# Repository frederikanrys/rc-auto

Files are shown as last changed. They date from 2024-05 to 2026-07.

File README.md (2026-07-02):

# Fri3d RC Car

This is a project to build a 3D printed remote controlled car. The car body is based on the classic Volkswagen Bus, reimagined as an off-road RC hot rod. The car is designed to be 3D printed and to be controlled by a remote control.

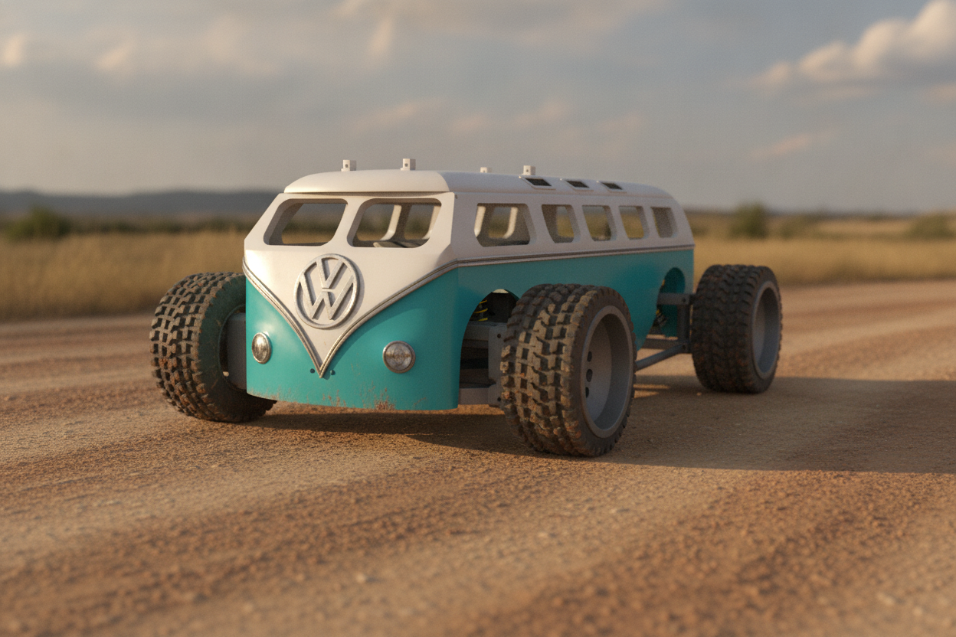
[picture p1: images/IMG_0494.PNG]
VW Bus


## Design Philosophy

The car uses off-the-shelf drivetrain components compatible with **Traxxas Slash 4x4** parts:

- **Differentials** - Metal differentials with bearings
- **Driveshafts** - CVD steel driveshafts and metal center driveshaft
- **Slipper Clutch** - Complete metal slipper clutch assembly
- **Drive Hubs** - Steel drive hub sets

This makes the car durable and easy to repair with widely available RC car parts.

## Parts List

### Motor & Electronics

| Item | Description | Link | Price | Qty |
| --- | --- | --- | ----- | --- |
| Motor + ESC | Pulsar B-20 or B-40 | <a href="https://nl.aliexpress.com/item/1005006742987156.html" target="_blank" rel="noopener noreferrer">AliExpress</a> | ~€30  | 1 |
| Pinion | 12T, 15T, or 20T | <a href="https://www.absima.shop/pp/alu-pinion-32dp/module0-8-20T.htm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" target="_blank" rel="noopener noreferrer">Absima</a> | ~€5 | 1 |
| Battery | 5200mAh, 2S, 80C | <a href="https://www.amazon.de/-/en/dp/B08X4GF9DK" target="_blank" rel="noopener noreferrer">Amazon</a> | ~€30  | 1 |
| Servo | | <a href="https://nl.aliexpress.com/item/1005007301836255.html" target="_blank" rel="noopener noreferrer">AliExpress</a> | ~€10  | 1 |
| Receiver + Transmitter | | | | 1 |

### Drivetrain (Differentials, Driveshafts & Slipper Clutch)

| Item | Description | Link | Price | Qty |
| --- | --- | --- | --- | --- |
| Differential (2pcs) | Front/Rear Differential with Bearing for Slash 4X4 VXL Stampede Rustler | <a href="https://www.aliexpress.com/item/1005007378476905.html" target="_blank" rel="noopener noreferrer">AliExpress</a> | ~€12 | 1 |
| Rear Ring Gear 6879 | Rear Differential Ring Gear G4713 6879 for Traxxas Slash 4X4 | <a href="https://www.aliexpress.com/item/32948469179.html" target="_blank" rel="noopener noreferrer">AliExpress</a> | ~€2 | 1 |
| Front Ring Gear G4513 | Front Differential Ring Gear G4513 for Traxxas Slash 4x4 | <a href="https://www.aliexpress.com/item/32952095481.html" target="_blank" rel="noopener noreferrer">AliExpress</a> | ~€6 | 1 |
| CVD Driveshaft (Front & Rear) | GRC Extreme Heavy Duty CVD U-Joint Steel Driveshaft for Traxxas Slash/Stampede/Hoss/Rustler VXL 4X4 Platinum Ultimate Update Parts, Replace #6851 - used for both front and rear (sold in packs of 2, need 2 packs) | <a href="https://www.temu.com/goods.html?goods_id=605796830151694&sku_id=92876117669400" target="_blank" rel="noopener noreferrer">Temu</a> | ~€13.50/pack | 2 |
| Center Driveshaft 6855 | Metal Center Driveshaft 6855 for Traxxas Slash 4X4 4WD Rally (Red) | <a href="https://www.aliexpress.com/item/1005005894739029.html" target="_blank" rel="noopener noreferrer">AliExpress</a> | ~€3 | 1 |
| Drive Hub Set Front | Steel Drive Hub Set for Traxxas Slash 4X4 VXL/Rustler/Stampede/XO-1 (**Front** **only**) | <a href="https://www.aliexpress.com/item/1005009469068869.html" target="_blank" rel="noopener noreferrer">AliExpress</a> | ~€2 | 1 |
| Slipper Clutch | Complete Slipper Clutch Assembly for Traxxas Slash Stampede 4X4 Rally | <a href="https://www.aliexpress.com/item/1005007927630121.html" target="_blank" rel="noopener noreferrer">AliExpress</a> | ~€8 | 1 |
| Motor Mount | Adjustable Motor Mounting Bracket Holder for 540/3660/3650 Brushless Motors | <a href="https://nl.aliexpress.com/item/4000424368907.html" target="_blank" rel="noopener noreferrer">AliExpress</a> | ~€4 | 1 |

### Bearings

| Item | Description | Link | Price | Qty |
| ---- | --- | ---- | ----- | --- |
| Bearing 5x11x4mm | MR115-2RS Bearing 10pcs 5x11x4mm Steel Double Shielded | <a href="https://nl.aliexpress.com/item/32824707297.html" target="_blank" rel="noopener noreferrer">AliExpress</a> | ~€4 | 1 |
| Bearing 6x12x4mm | MR126RS Bearing 10pcs 6x12x4mm ABEC-7 Blue Sealed | <a href="https://www.aliexpress.com/item/1005006083328247.html" target="_blank" rel="noopener noreferrer">AliExpress</a> | ~€4 | 1 |
| Bearing 10x15x4mm | 6700-2RS Bearing 10pcs 10x15x4mm ABEC-3 Blue Sealed | <a href="https://nl.aliexpress.com/item/32904604356.html" target="_blank" rel="noopener noreferrer">AliExpress</a> | ~€4 | 1 |
| Bearing 12x18x4mm | 6701-2RS Bearing 10pcs 12x18x4mm ABEC-7 Blue Sealed | <a href="https://www.aliexpress.com/item/1005006475668561.html" target="_blank" rel="noopener noreferrer">AliExpress</a> | ~€4 | 1 |

### Fasteners & Hardware

| Item | Description | Link | Price | Qty |
| --- | --- | --- | ----- | --- |
| Screw Bolt Set M3 | M2 M3 M4 Screw Bolt Set for RC Crawler Bumper Driveshaft Pin | <a href="https://www.aliexpress.com/item/1005009800470993.html" target="_blank" rel="noopener noreferrer">AliExpress</a> | ~€2 | 1 |
| Lock Nuts M5 | 304/316 Stainless Steel Flange Nylon Lock Nuts M5 Serrated (20pcs) | <a href="https://www.aliexpress.com/item/1005009771309255.html" target="_blank" rel="noopener noreferrer">AliExpress</a> | ~€2 | 1 |
| Dowel Pins M2 | GB119 Cylindrical Dowel Pins M2 304 Stainless Steel (50pcs, 10mm)  | <a href="https://www.aliexpress.com/item/1005007023343232.html" target="_blank" rel="noopener noreferrer">AliExpress</a> | ~€2 | 1 |
| Heat Insert Nuts M3 | Brass Heat Insert Nuts M3xL5xOD4.5 for 3D Printing (50pcs) | <a href="https://www.aliexpress.com/item/1005006472702418.html" target="_blank" rel="noopener noreferrer">AliExpress</a> | ~€2 | 1 |
| Screws M3 | M3 Hex Socket Screws Set (440pcs) | <a href="https://www.amazon.de/-/nl/dp/B0B3MGZ7T2" target="_blank" rel="noopener noreferrer">Amazon</a> | ~€10  | 1 |
| Body Shell Clips | MJX Hyper Go R-type Body Shell Clips Pin (24pcs) | <a href="https://www.aliexpress.com/item/1005009096269708.html" target="_blank" rel="noopener noreferrer">AliExpress</a> | ~€2 | 1 |

## Printed Parts

Depending on the print settings, you will need around 2KG of Filament to print all the parts. Instead of PLA, you can also use PETG or ABS.

For TPU parts (except tires), we recommend <a href="https://extrudr.com/en/at/products/flex-hard/" target="_blank" rel="noopener noreferrer">Extrudr Flex Hard</a> for better impact absorption.

| Part | Material | Qty | Notes |
|---|---|-----|---|
| <a href="files/plate-front-bottom.stl" target="_blank" rel="noopener noreferrer">Plate - front - bottom</a> | PLA | 1 | |
| <a href="files/plate-rear-bottom.stl" target="_blank" rel="noopener noreferrer">Plate - rear - bottom</a> | PLA | 1 | |
| <a href="files/plate-diff-front-top.stl" target="_blank" rel="noopener noreferrer">Plate - diff - front - top</a> | PLA | 1 | **100% infill** |
| <a href="files/plate-diff-rear-top.stl" target="_blank" rel="noopener noreferrer">Plate - diff - rear - top</a> | PLA | 1 | **100% infill** |
| <a href="files/plate-battery-holder.stl" target="_blank" rel="noopener noreferrer">Plate - battery - holder</a> | PLA | 1 | |
| <a href="files/wing-bottom.stl" target="_blank" rel="noopener noreferrer">Wing - bottom</a> | PLA/TPU-A98 | 4 | TPU for impact |
| <a href="files/wing-top.stl" target="_blank" rel="noopener noreferrer">Wing - top</a> | PLA/TPU-A98 | 4 | TPU for impact |
| <a href="files/turn-caster-front.stl" target="_blank" rel="noopener noreferrer">Turn - caster - front</a> | PLA | 2 | **100% infill** |
| <a href="files/turn-caster-rear.stl" target="_blank" rel="noopener noreferrer">Turn - caster - rear</a> | PLA | 2 | **100% infill** |
| <a href="files/turn-front.stl" target="_blank" rel="noopener noreferrer">Turn - front</a> | PLA | 2 | **100% infill** |
| <a href="files/steering-left.stl" target="_blank" rel="noopener noreferrer">Steering - left</a> | PLA | 1 | |
| <a href="files/steering-right.stl" target="_blank" rel="noopener noreferrer">Steering - right</a> | PLA | 1 | |
| <a href="files/steering-connect.stl" target="_blank" rel="noopener noreferrer">Steering - connector</a> | PLA/TPU-A95 | 1 | TPU = servo saver |
| <a href="files/steering-rings.stl" target="_blank" rel="noopener noreferrer">Steering - rings</a> | PLA | 2 | |
| <a href="files/steering-top.stl" target="_blank" rel="noopener noreferrer">Steering - top</a> | PLA | 1 | |
| <a href="files/steering-arm-75mm.stl" target="_blank" rel="noopener noreferrer">Steering - rod - 75mm</a> | PLA/TPU-A95 | 2 | TPU = servo saver |

### VW Bus Body

| Part | Material | Qty | Notes |
|---|---|-----|---|
| <a href="files/vw-bus/bus-front.3mf" target="_blank" rel="noopener noreferrer">Bus - front</a> | PLA/PETG | 1 | |
| <a href="files/vw-bus/bus-rear.3mf" target="_blank" rel="noopener noreferrer">Bus - rear</a> | PLA/PETG | 1 | |
| <a href="files/vw-bus/roof-front.stl" target="_blank" rel="noopener noreferrer">Roof - front</a> | PLA/PETG | 1 | |
| <a href="files/vw-bus/roof-rear.stl" target="_blank" rel="noopener noreferrer">Roof - rear</a> | PLA/PETG | 1 | |
| <a href="files/vw-bus/nose.stl" target="_blank" rel="noopener noreferrer">Nose</a> | PLA/PETG | 1 | |
| <a href="files/vw-bus/logo.stl" target="_blank" rel="noopener noreferrer">Logo</a> | PLA/PETG | 1 | |
| <a href="files/vw-bus/light.stl" target="_blank" rel="noopener noreferrer">Light</a> | PLA/PETG | 1 | |
| <a href="files/vw-bus/rail-nose-left.stl" target="_blank" rel="noopener noreferrer">Rail - nose - left</a> | PLA/PETG | 1 | |
| <a href="files/vw-bus/rail-nose-right%20.stl" target="_blank" rel="noopener noreferrer">Rail - nose - right</a> | PLA/PETG | 1 | |
| <a href="files/vw-bus/rail-front-left.stl" target="_blank" rel="noopener noreferrer">Rail - front - left</a> | PLA/PETG | 1 | |
| <a href="files/vw-bus/rail-front-right.stl" target="_blank" rel="noopener noreferrer">Rail - front - right</a> | PLA/PETG | 1 | |
| <a href="files/vw-bus/rail-rear-left%20.stl" target="_blank" rel="noopener noreferrer">Rail - rear - left</a> | PLA/PETG | 1 | |
| <a href="files/vw-bus/rail-rear-right.stl" target="_blank" rel="noopener noreferrer">Rail - rear - right</a> | PLA/PETG | 1 | |

### Optional Printed Parts

These parts can also be bought off the shelf.

| Part | Material | Qty | Notes |
|---|---|-----|---|
| <a href="files/shock.stl" target="_blank" rel="noopener noreferrer">Shock</a> | PLA | 8 | Slider and cap |
| <a href="files/wheel-tire.stl" target="_blank" rel="noopener noreferrer">Wheel - tire</a> | TPU-A95 | 4 | |
| <a href="files/wheel-rim.stl" target="_blank" rel="noopener noreferrer">Wheel - rim</a> | PLA | 4 | |
| <a href="files/wheel-hex.stl" target="_blank" rel="noopener noreferrer">Wheel - hex</a> | PLA | 4 | |

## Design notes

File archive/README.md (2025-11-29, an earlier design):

# Fri3d RC Car (Archive)

> **Note:** This is the archived version of the original Fri3d RC Car design. For the latest version with Traxxas Slash 4x4 compatible drivetrain components, see the [main project](../README.md).

This is a project to build a 3D printed remote controlled car. The car body is based on the [Cybertruck](https://www.tesla.com/cybertruck) from Tesla. The car is designed to be 3D printed and to be controlled by a remote control.

As this is not a beginner project, it is recommended to have some experience with 3D printing and remote controlled cars.
The project is an open-source project and can be used by anyone. We originally designed this project for [Fri3d Camp](https://fri3d.be/) to build 5 cars with children and play with them during the camp.

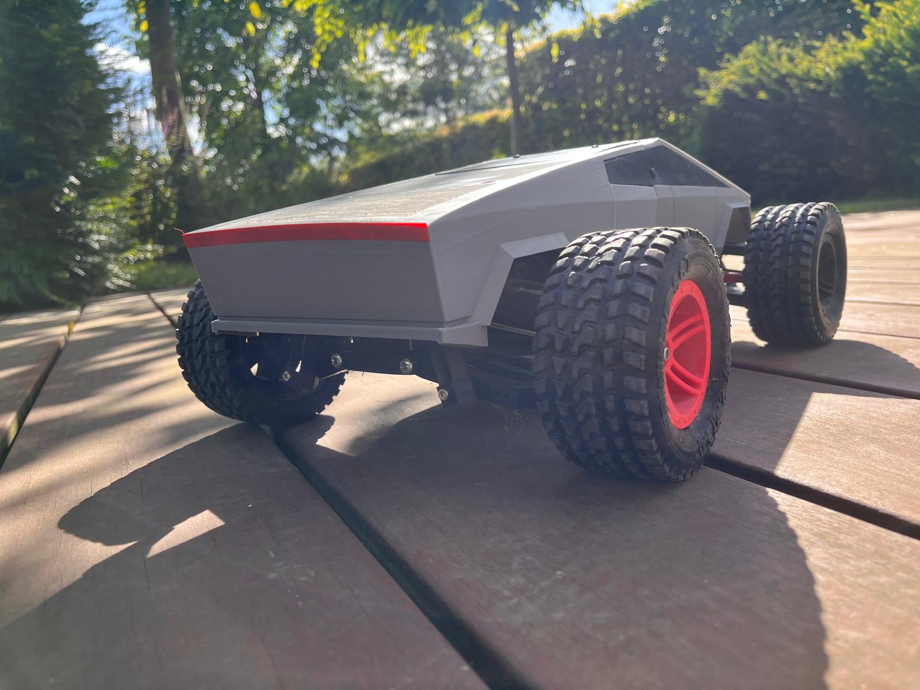
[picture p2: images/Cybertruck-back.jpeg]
Cybertruck


# How to start?
There is a combination of printed parts and off the shelf parts. Both off the shelf parts and printed parts are listed in the [Bill of Material](#Bill-of-Material). Off the shelf parts can be bought from various online stores such as the one proposed in the Link column.
The printed parts are available in the [stl](stl) directory. The original design files are available in the [shapr](shapr) directory.
The printed parts can be printed on a printer with a maximum size of 25cm x 25cm x 25cm. Most parts can be printed with PLA, but some parts are to be printed with TPU (to absorb impact).

The car is designed with durability in mind. You will notice we do not print the parts that need to be very strong such as the differentials and dog bones. You should buy them online. It makes the car a bit more expensive to build, but it will last much longer. 
For more durability, some parts are to be printed in TPU (flexible filament). i.e.: the bumper, the caster claws, and the top and bottom of the wings,... 
That way, they can absorb the impact of a crash without breaking.

# Assembly
Once you have the printed the parts on your printer and bought some of the parts online, you can start to assemble the car as described in the following documents:
1. [Part 1 - Body](manual/part1-body.pdf) 
2. [Part 2 - Front & Back](manual/part2-front-back.pdf)
3. [Part 3 - Final](manual/part3-final.pdf)

Happy assembling and Good Luck!

# Bill of Material
## Off the shelf parts
| Description | # | Comment | Link |
| --- | --- | --- | --- |
| Motor + ESC | 1 | Test Pulsar B-20, B-40 | [aliexpress.com](https://nl.aliexpress.com/item/1005006742987156.html) |
| Motor Mount | 1 | | |
| Pinion | 1 | 12T, 15T, 20T | [absima.be](https://www.absima.shop/pp/alu-pinion-32dp/module0-8-20T.htm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) |
| Battery | 1 | 5200mAh, 2S, 80C | [amazon.de](https://www.amazon.de/-/en/dp/B08X4GF9DK?psc=1&ref=ppx_yo2ov_dt_b_product_details) |
| Servo | 1 | | [aliexpress.com](https://nl.aliexpress.com/item/1005007301836255.html) |
| Receiver + Transmitter | 1 | | |
| Bearing - 10X15X4 | 8 | | |
| Bearing - 5X10X4 | 8 | | |
| Screws M3 | 1 | 440 pieces | [Amazon.de](https://www.amazon.de/-/nl/dp/B0B3MGZ7T2/ref=pd_day0fbt_thbs_d_sccl_2/257-0877788-9470555) |
| Screws M4 (100mm or 70mm) | 4 | Bottom wing - plate connection | |
| Wheel Fastener | 4 | | |
| Threaded inserts | 8 | Diff cover | |
| Rubber band | 4 | Shock | |

## Printed parts
Depending on the print settings, you will need around 2KG of Filament to print all the parts. Instead of PLA, you can also use PETG or ABS.

| Check | Description | Material | # | Comment |
| --- | --- | --- | --- | --- |
| <span style="color: green;">&#10004;</span> | Receiver box | PLA | 1 | Will use OOTB |
| | Servo - steering rod | | 1 | |
| | | | | |
| <span style="color: green;">&#10004;</span> | [Wheel - tire](stl/wheel-tire.stl) | TPU-A95 | 4 | Last set of 4 are from test vehicle |
| <span style="color: green;">&#10004;</span> | [Wheel - rim](stl/wheel-rim.stl) | PLA | 4 | Last set of 4 are from test vehicle |
| | [Wheel - hex](stl/wheel-hex.stl) | PLA | 4 | Still need to make 2mmx1cm hex pins |
| <span style="color: green;">&#10004;</span> | [Plate - center](stl/plate-center.stl) | PLA | 1 | 3 cannot handle long M4 x 100mm, 2 have a minor defect on top |
| <span style="color: green;">&#10004;</span> | [Plate - front](stl/plate-bottom-front.stl) | PLA | 1 | |
| <span style="color: green;">&#10004;</span> | [Plate - rear](stl/plate-bottom-rear.stl) | PLA | 1 | |
| <span style="color: green;">&#10004;</span> | [Plate - Diff - top](stl/plate-diff-top.stl) | PLA | 2 | Print with 100% fill rate |
| <span style="color: green;">&#10004;</span> | [Plate - battery - holder](stl/plate-battery-holder.stl) | PLA | 1 | |
| <span style="color: green;">&#10004;</span> | [Wing - bottom](stl/wing-bottom.stl) | PLA or TPU-A98 | 4 | Use TPU to absorb impact |
| <span style="color: green;">&#10004;</span> | [Wing - top](stl/wing-top.stl) | PLA or TPU-A98 | 4 | Use TPU to absorb impact |
| | [Caster - claw](stl/turn-caster) | TPU-A98 | 4 | Use TPU to absorb impact |
| | [Caster - turning](stl/turn-front) | PLA | 2 | |
| | [Caster - fixed](stl/turn-rear) | PLA | 2 | |
| <span style="color: green;">&#10004;</span> | [Shock - slider](stl/Shock.stl) | PLA | 8 | |
| <span style="color: green;">&#10004;</span> | [Shock - cap](stl/Shock.stl) | PLA | 8 | |
| <span style="color: green;">&#10004;</span> | [Steer - turn-left](stl/steering-left.stl) | PLA | 1 | |
| <span style="color: green;">&#10004;</span> | [Steer - turn-right](stl/steering-right.stl) | PLA | 1 | |
| <span style="color: green;">&#10004;</span> | [Steer - connector](stl/steering-connect.stl) | PLA or TPU-A95 | 1 | TPU acts as servo saver |
| <span style="color: green;">&#10004;</span> | [Steer - rings](stl/steering-rings.stl) | PLA | 2 | |
| <span style="color: green;">&#10004;</span> | [Steer - top](stl/steering-top.stl) | PLA | 1 | |
| <span style="color: green;">&#10004;</span> | [Steer - rod - 67mm](stl/steering-arm-67mm.stl) | PLA or TPU-A95 | 2 | TPU acts as servo saver |
| <span style="color: green;">&#10004;</span> | [Driveshaft - bearing](stl/driveshaft-bearing-28x12.5x8.stl) | PLA | 1 | |
| | [Driveshaft - gear 48T](stl/driveshaft-gear-48T.stl) | PLA | 1 | Print with 100% fill rate |
| <span style="color: green;">&#10004;</span> | [Driveshaft - gear 60T](stl/driveshaft-gear-60T.stl) | PLA | 1 | Print with 100% fill rate |
| <span style="color: green;">&#10004;</span> | [Driveshaft - axle](stl/driveshaft.stl) | PLA or ABS | 1 | Print with 100% fill rate |
| <span style="color: green;">&#10004;</span> | [Bumper](stl/bumper.stl) | TPU-A95 | 1 | Use TPU to absorb impact |
| <span style="color: green;">&#10004;</span> | [Cybertruck - front](stl/Cybertruck-front.stl) | PLA | 1 | |
| <span style="color: green;">&#10004;</span> | [Cybertruck - front - holder](stl/Cybertruck-front-holder.stl) | PLA | 1 | |
| <span style="color: green;">&#10004;</span> | [Cybertruck - rear](stl/Cybertruck-rear.stl) | PLA | 1 | |
| <span style="color: green;">&#10004;</span> | [Cybertruck - rear - holder](stl/Cybertruck-rear-holder.stl) | PLA | 1 | |
| <span style="color: green;">&#10004;</span> | [Cybertruck - decal](stl/Cybertruck-decal.stl) | PLA | 1 | |
| <span style="color: green;">&#10004;</span> | [Cybertruck - logo](stl/Cybertruck-logo.stl) | PLA | 1 | |

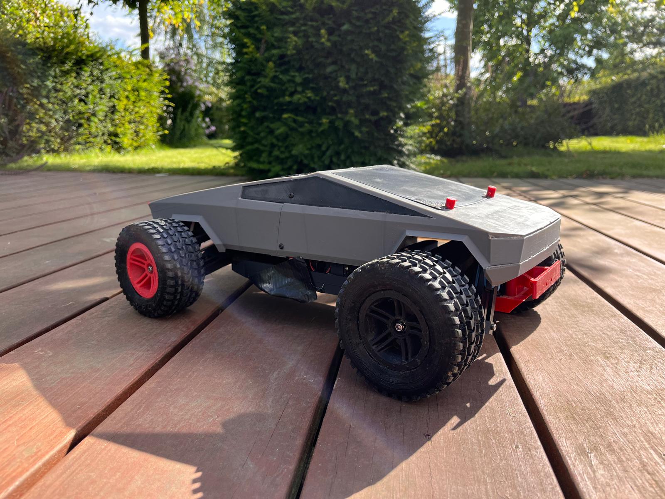
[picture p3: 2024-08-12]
images/Cybertruck-front.jpeg

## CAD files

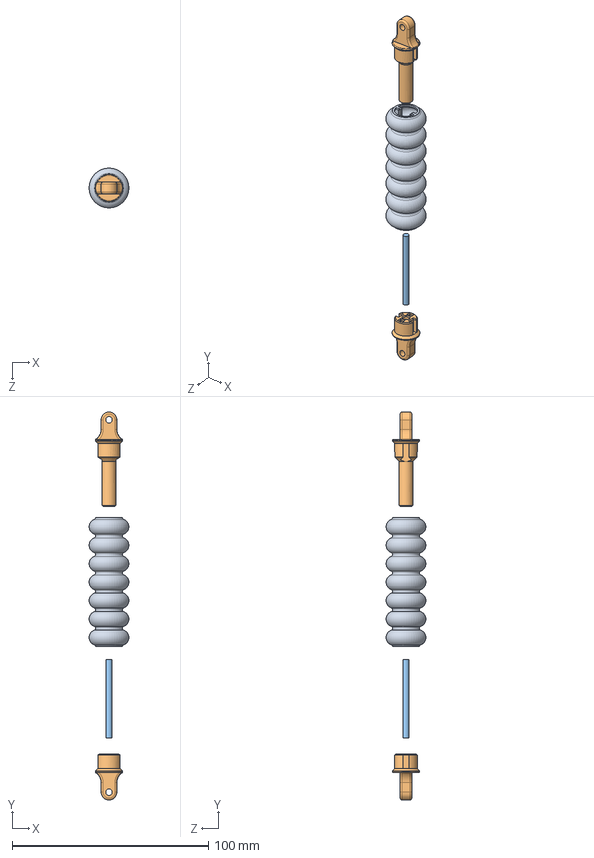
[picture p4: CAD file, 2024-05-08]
shapr/shocks/TPU Shocks/shock-assy-V2.SLDASM
20.3 x 197.6 x 20.3 mm
tpu-spring
shock-eye x 2
shock-pin

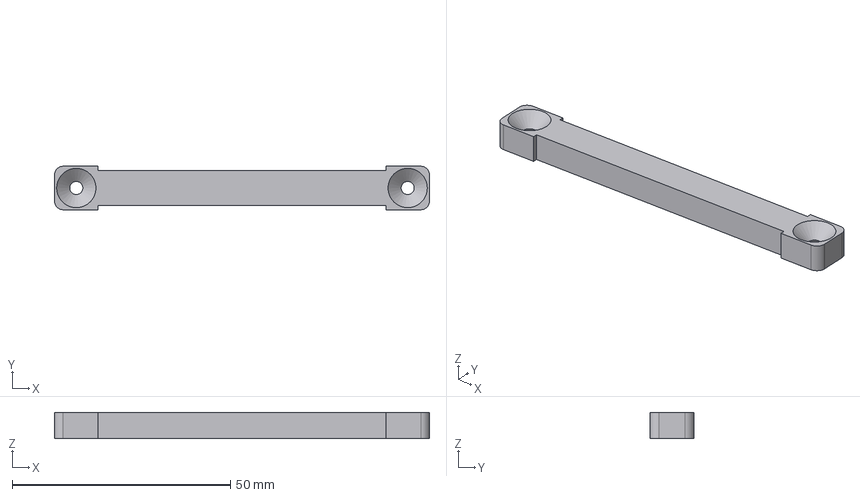
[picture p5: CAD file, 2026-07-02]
files/originals/SteerArm.step
86.0 x 10.0 x 6.00 mm

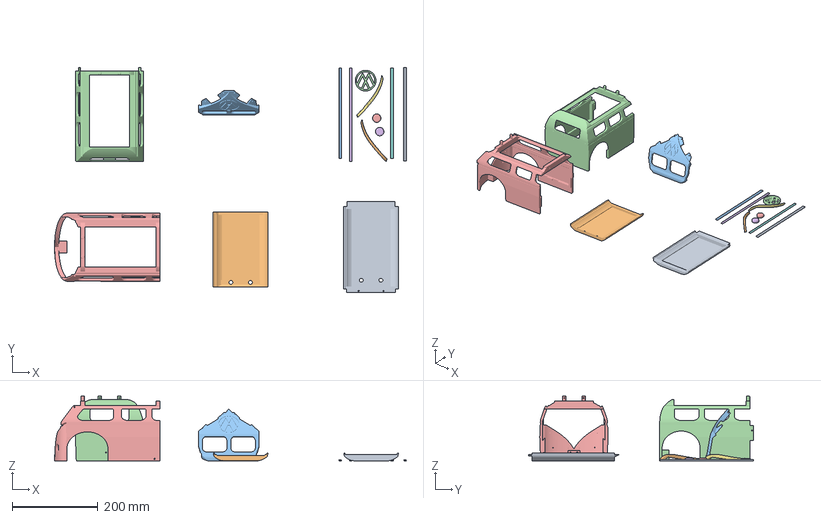
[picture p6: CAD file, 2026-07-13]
files/vw-bus/vw-bus-print-plate.3mf
821.7 x 525.9 x 151.5 mm
roof-rear.stl
roof-front.stl
nose.stl
bus-rear
bus-front
rail-front-right.stl
rail-nose-right .stl
rail-rear-right.stl
rail-front-left.stl
rail-nose-left.stl
rail-rear-left .stl
logo.stl
light.stl x 2

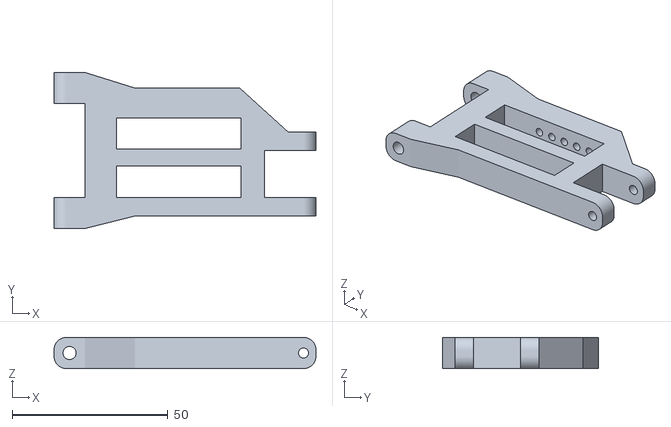
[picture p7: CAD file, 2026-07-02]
files/wing-bottom.stl
84.0 x 50.0 x 10.0

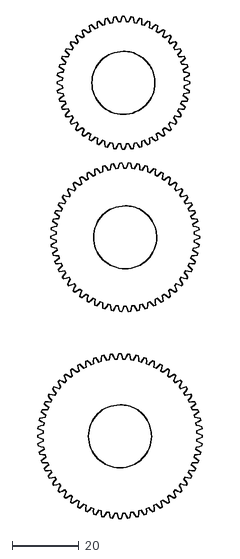
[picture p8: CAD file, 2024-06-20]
shapr/util/gears.dxf
49.3 x 150.4

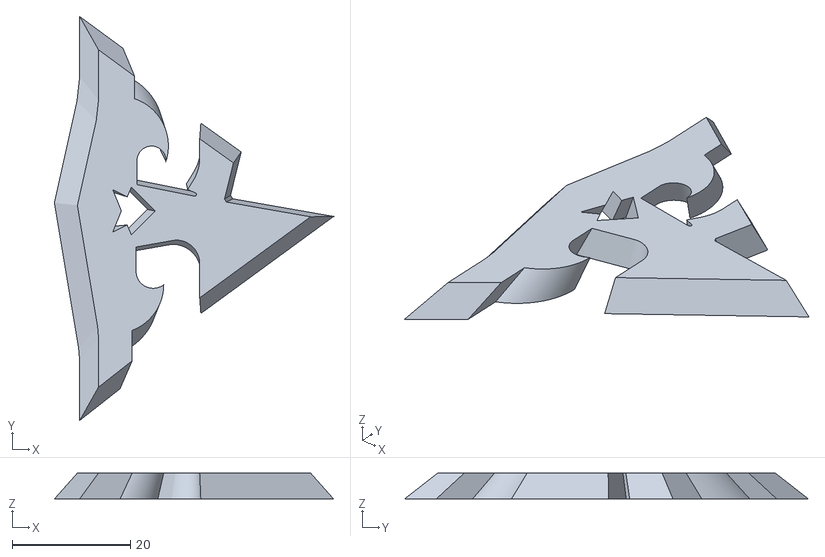
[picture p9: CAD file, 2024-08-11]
stl/Cybertruck-logo.stl
47.3 x 68.5 x 4.40

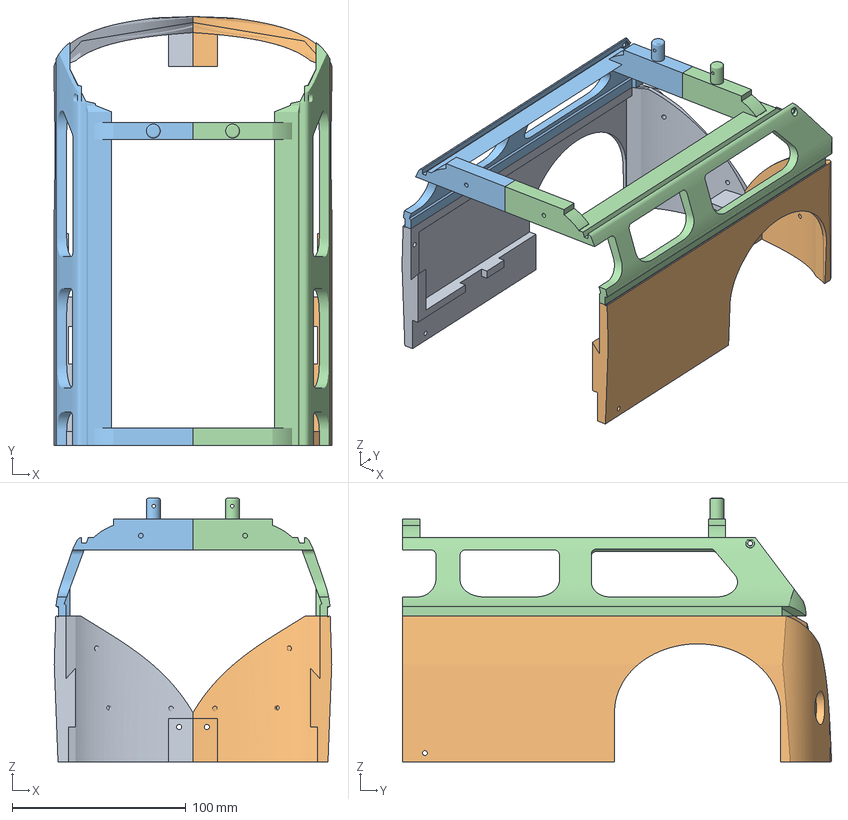
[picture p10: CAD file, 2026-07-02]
files/vw-bus/bus-front.3mf
159.6 x 246.7 x 151.5 mm

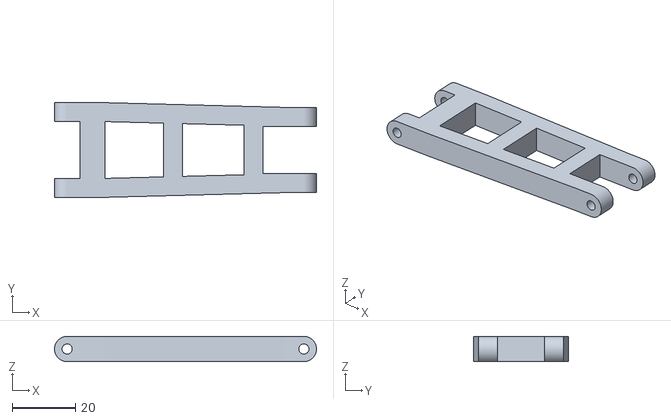
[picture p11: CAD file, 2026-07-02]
files/wing-top.stl
83.0 x 30.0 x 8.00

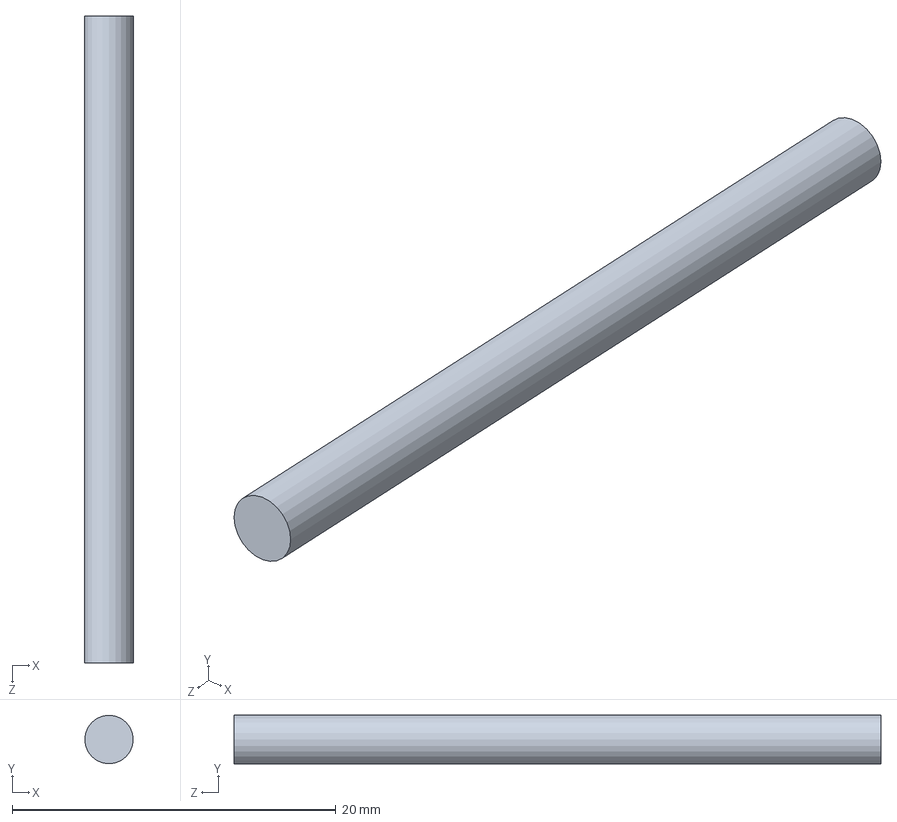
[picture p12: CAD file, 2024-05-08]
shapr/shocks/TPU Shocks/shock-pin.SLDPRT
3.00 x 3.00 x 40.0 mm

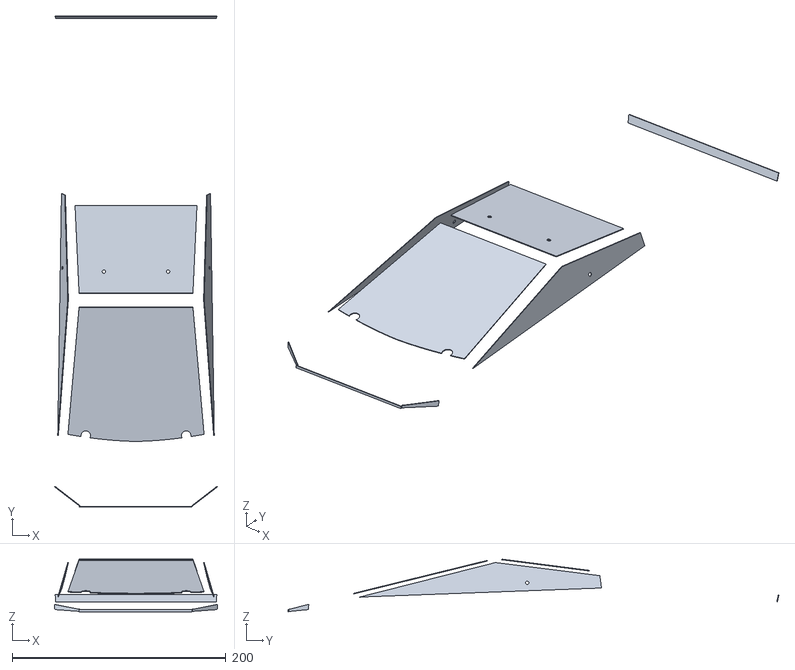
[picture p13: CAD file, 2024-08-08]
stl/Cybertruck-decal.stl
152.7 x 459.8 x 49.4

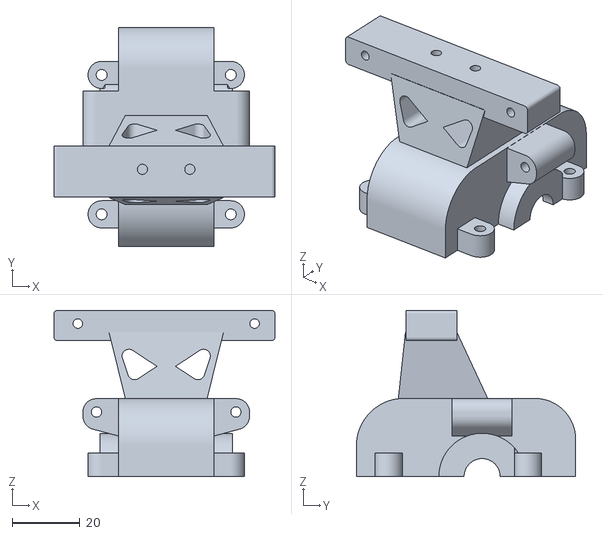
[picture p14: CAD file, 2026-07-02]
files/plate-diff-rear-top.stl
65.0 x 64.5 x 48.9

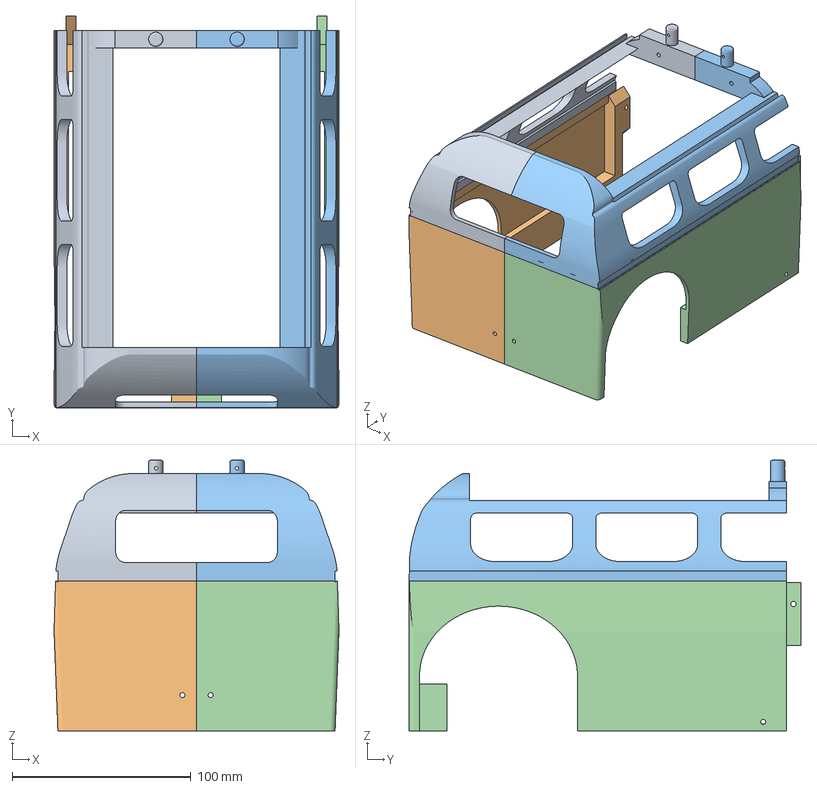
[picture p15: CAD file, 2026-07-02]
files/vw-bus/bus-rear.3mf
159.6 x 219.4 x 151.5 mm

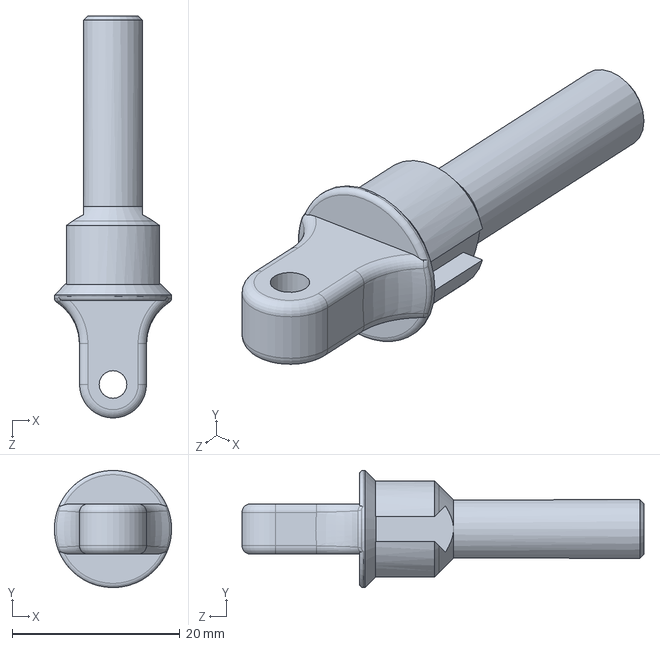
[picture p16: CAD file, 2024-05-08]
shapr/shocks/TPU Shocks/shock-eye.SLDPRT
14.0 x 14.0 x 48.0 mm

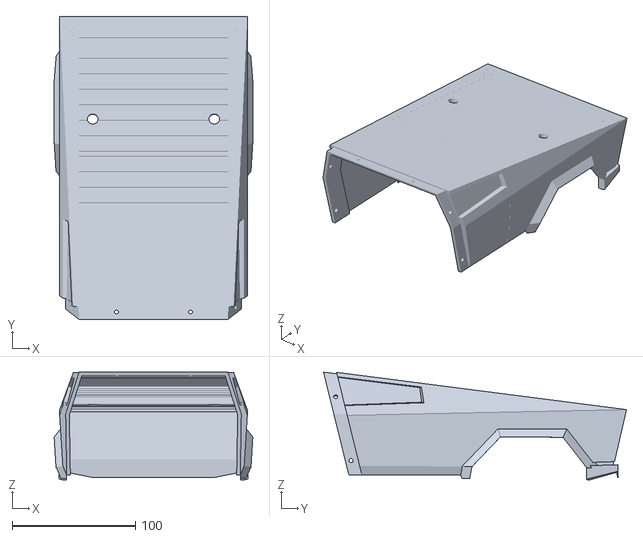
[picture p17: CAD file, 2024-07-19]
stl/Cybertruck-rear.stl
161.3 x 246.0 x 87.5

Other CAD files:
files/plate-rear-bottom.stl
files/vw-bus/logo.stl
stl/plate-center.stl
files/turn-caster-front.stl
archive/shapr/shocks/OpenRC Shocks/STL/Body.stl
archive/shapr/shocks/OpenRC Shocks/STL/Bottom.stl
archive/shapr/shocks/OpenRC Shocks/STL/Lid.stl
archive/shapr/shocks/OpenRC Shocks/STL/Spring.stl
archive/shapr/shocks/OpenRC Shocks/STP/Body.stp
archive/shapr/shocks/OpenRC Shocks/STP/Bottom.stp
archive/shapr/shocks/OpenRC Shocks/STP/Lid.stp
archive/shapr/shocks/OpenRC Shocks/STP/Open RC Experimental Shock Assembly.stp
archive/shapr/shocks/OpenRC Shocks/STP/Spring.stp
archive/shapr/shocks/TPU Shocks/shock-assy.SLDDRW
archive/stl/Cybertruck-front-holder.stl
archive/stl/Cybertruck-front.stl
archive/stl/Cybertruck-rear-holder.stl
archive/stl/driveshaft-gear-48T.stl
archive/stl/driveshaft-gear-60T.stl
archive/stl/driveshaft.stl
archive/stl/plate-bottom-front.stl
archive/stl/plate-bottom-rear.stl
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

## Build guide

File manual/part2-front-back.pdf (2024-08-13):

# FR0NT

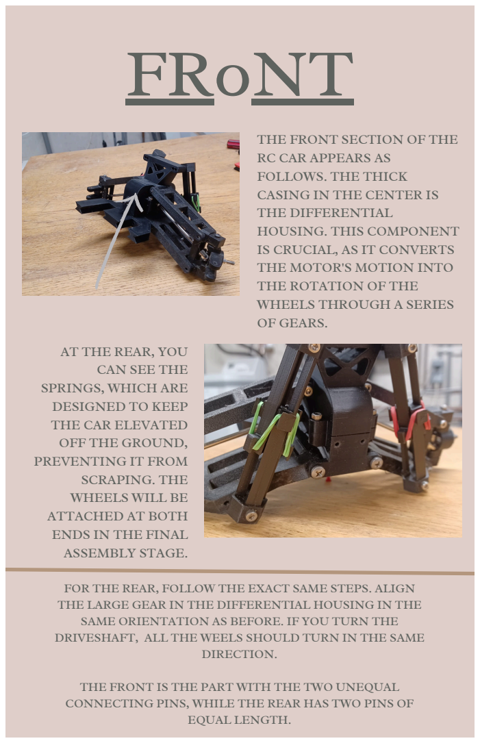
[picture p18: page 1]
DIRECTION.; EQUAL LENGTH.

THE FRONT SECTION OF THE
RC CAR APPEARS AS
FOLLOWS. THE THICK
CASING IN THE CENTER IS
THE DIFFERENTIAL
HOUSING. THIS COMPONENT
IS CRUCIAL, AS IT CONVERTS
THE MOTOR'S MOTION INTO
THE ROTATION OF THE
WHEELS THROUGH A SERIES
OF GEARS.

AT THE REAR, YOU
CAN SEE THE

SPRINGS, WHICH ARE
DESIGNED TO KEEP
THE CAR ELEVATED
OFF THE GROUND,
PREVENTING IT FROM
SCRAPING. THE
WHEELS WILL BE
ATTACHED AT BOTH
ENDS IN THE FINAL
ASSEMBLY STAGE.

FOR THE REAR, FOLLOW THE EXACT SAME STEPS. ALIGN
THE LARGE GEAR IN THE DIFFERENTIAL HOUSING IN THE
SAME ORIENTATION AS BEFORE. IF YOU TURN THE
DRIVESHAFT, ALL THE WEELS SHOULD TURN IN THE SAME

THE FRONT IS THE PART WITH THE TWO UNEQUAL
CONNECTING PINS, WHILE THE REAR HAS TWO PINS OF

# STEP 1

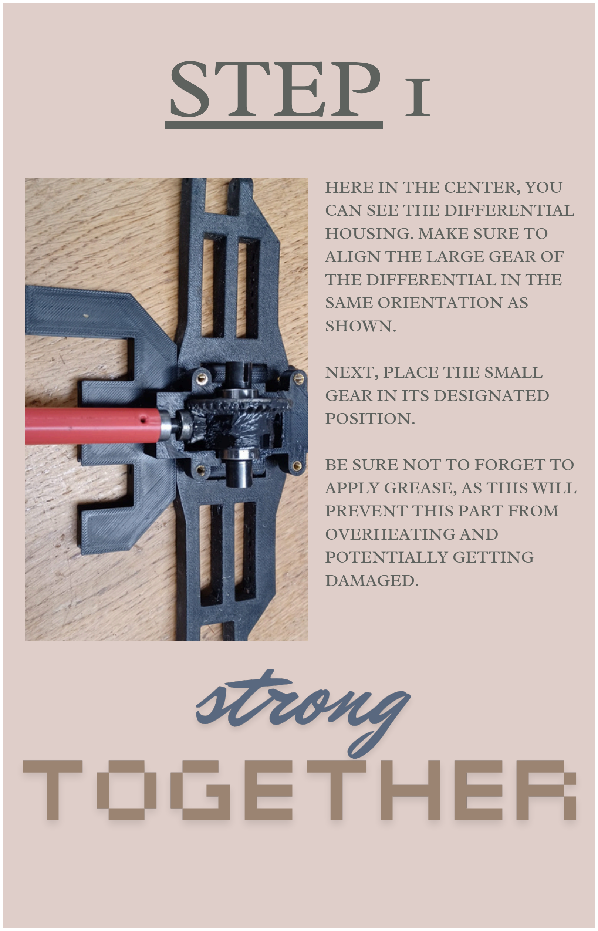
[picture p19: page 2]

HERE IN THE CENTER, YOU
CAN SEE THE DIFFERENTIAL
HOUSING. MAKE SURE TO
ALIGN THE LARGE GEAR OF
THE DIFFERENTIAL IN THE
SAME ORIENTATION AS
SHOWN.

NEXT, PLACE THE SMALL
GEAR IN ITS DESIGNATED
POSITION.

BE SURE NOT TO FORGET TO
APPLY GREASE, AS THIS WILL PREVENT THIS PART FROM
OVERHEATING AND
POTENTIALLY GETTING
DAMAGED.

# STEP 2

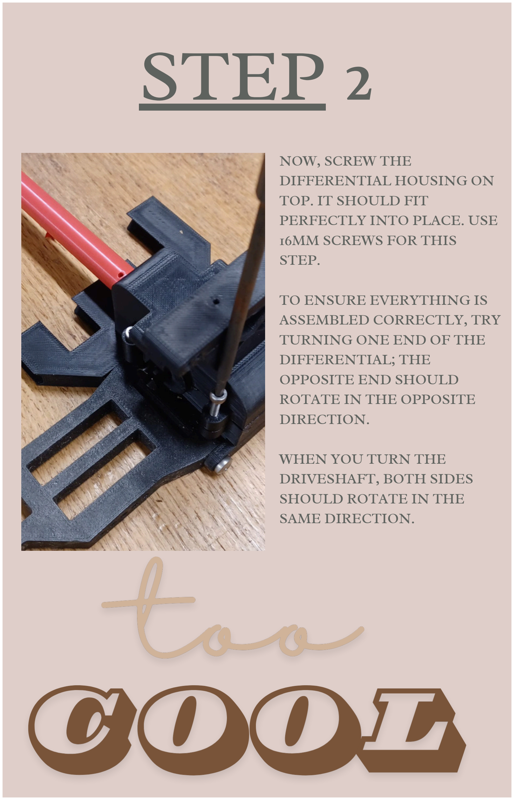
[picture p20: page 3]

NOW, SCREW THE
DIFFERENTIAL HOUSING ON
TOP. IT SHOULD FIT
PERFECTLY INTO PLACE. USE
16MM SCREWS FOR THIS
STEP.

TO ENSURE EVERYTHING IS
ASSEMBLED CORRECTLY, TRY
TURNING ONE END OF THE
DIFFERENTIAL; THE
OPPOSITE END SHOULD
ROTATE IN THE OPPOSITE
DIRECTION.

WHEN YOU TURN THE
DRIVESHAFT, BOTH SIDES
SHOULD ROTATE IN THE
SAME DIRECTION.

# STEP 3

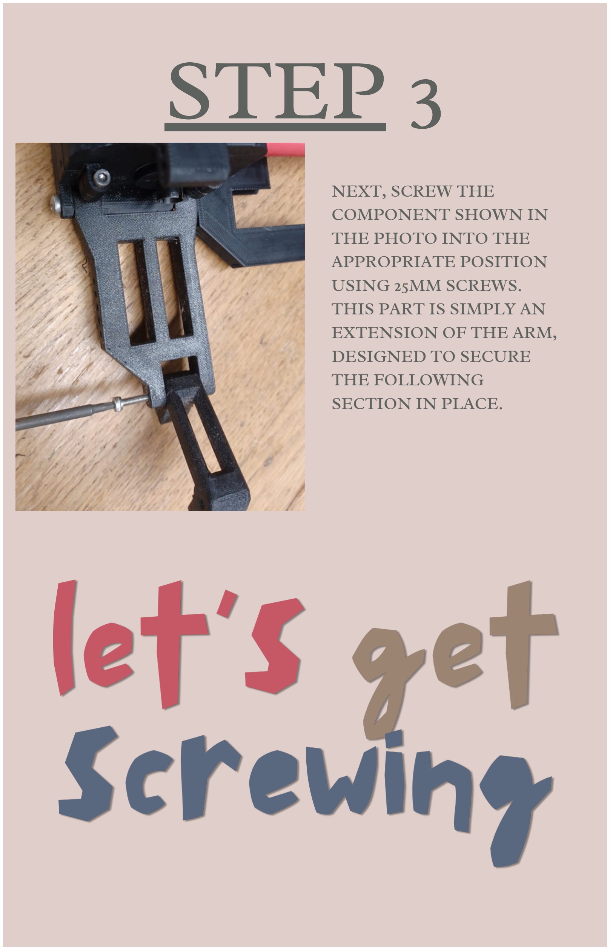
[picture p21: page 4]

NEXT, SCREW THE
COMPONENT SHOWN IN
THE PHOTO INTO THE
APPROPRIATE POSITION
USING 25MM SCREWS.
THIS PART IS SIMPLY AN
EXTENSION OF THE ARM,
DESIGNED TO SECURE
THE FOLLOWING
SECTION IN PLACE.

# STEP 4

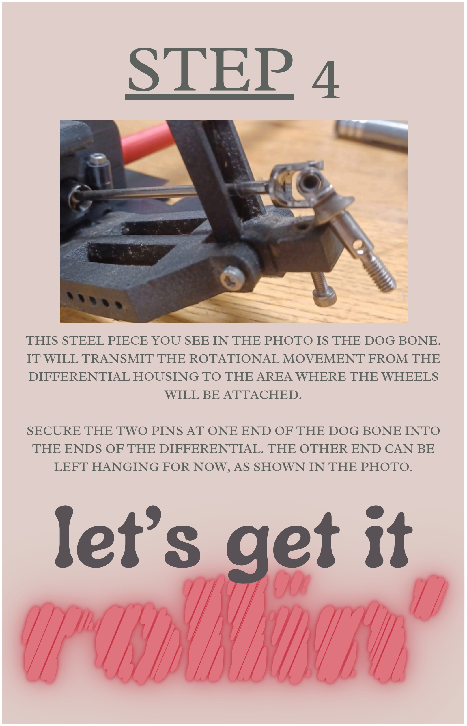
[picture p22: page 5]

THIS STEEL PIECE YOU SEE IN THE PHOTO IS THE DOG BONE. IT WILL TRANSMIT THE ROTATIONAL MOVEMENT FROM THE DIFFERENTIAL HOUSING TO THE AREA WHERE THE WHEELS WILL BE ATTACHED.

SECURE THE TWO PINS AT ONE END OF THE DOG BONE INTO THE ENDS OF THE DIFFERENTIAL. THE OTHER END CAN BE LEFT HANGING FOR NOW, AS SHOWN IN THE PHOTO.

# let’s get it

# STEP 5

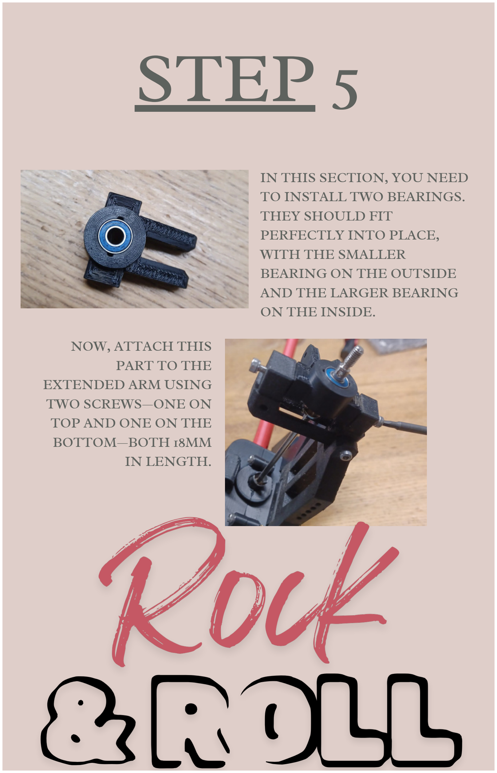
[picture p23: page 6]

IN THIS SECTION, YOU NEED
TO INSTALL TWO BEARINGS.
THEY SHOULD FIT
PERFECTLY INTO PLACE,
WITH THE SMALLER
BEARING ON THE OUTSIDE
AND THE LARGER BEARING
ON THE INSIDE.

NOW, ATTACH THIS
PART TO THE
EXTENDED ARM USING
TWO SCREWS—ONE ON
TOP AND ONE ON THE
BOTTOM—BOTH 18MM
IN LENGTH.

# STEP 6

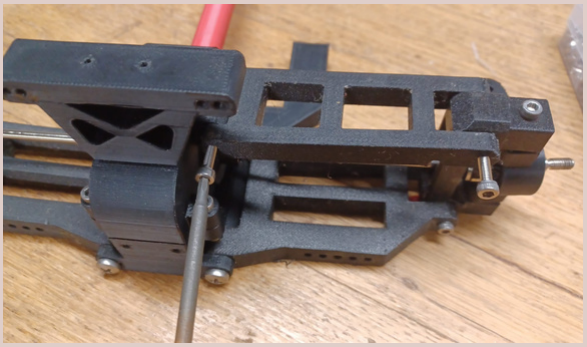
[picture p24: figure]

NOW, YOU'LL ATTACH THE UPPER ARM. THIS COMPONENT PROVIDES ADDITIONAL STABILITY AND HELPS KEEP EVERYTHING BALANCED. IT IS PERFECTLY SYMMETRICAL, SO THERE IS NO WRONG WAY TO POSITION IT. SECURE IT WITH A 30MM SCREW FROM THE TOP AND A 25MM SCREW FROM THE BOTTOM.

# great work!

# STEP 7

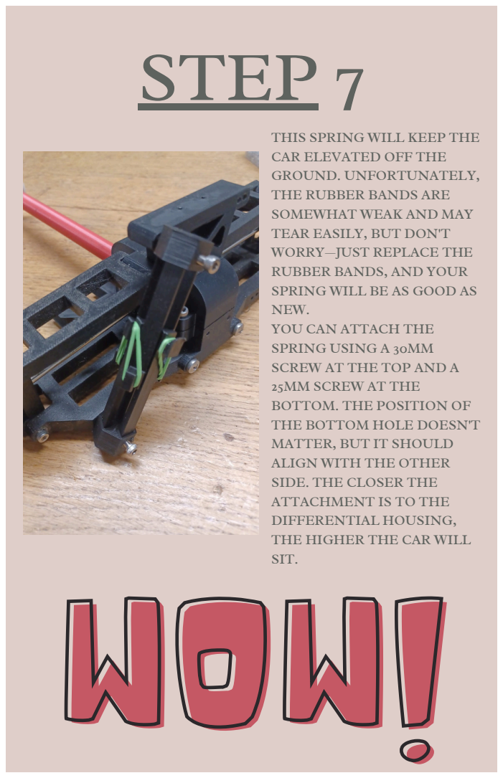
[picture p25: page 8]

THIS SPRING WILL KEEP THE
CAR ELEVATED OFF THE
GROUND. UNFORTUNATELY,
THE RUBBER BANDS ARE
SOMEWHAT WEAK AND MAY
TEAR EASILY, BUT DON'T
WORRY—JUST REPLACE THE
RUBBER BANDS, AND YOUR
SPRING WILL BE AS GOOD AS
NEW.
YOU CAN ATTACH THE
SPRING USING A 30MM
SCREW AT THE TOP AND A
25MM SCREW AT THE
BOTTOM. THE POSITION OF
THE BOTTOM HOLE DOESN'T
MATTER, BUT IT SHOULD
ALIGN WITH THE OTHER
SIDE. THE CLOSER THE
ATTACHMENT IS TO THE
DIFFERENTIAL HOUSING,
THE HIGHER THE CAR WILL
SIT.
WOW!

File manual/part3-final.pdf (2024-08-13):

# FINAL

YOU’RE ALMOST AT THE
END OF THIS GUIDE! IN
THIS FINAL STEP, WE’LL
FINISH UP THE LAST
DETAILS: CONNECTING
THE CABLES,
ATTACHING THE
WHEELS, AND TURNING
OUR RC CAR INTO A
TRUE TESLA
CYBERTRUCK.

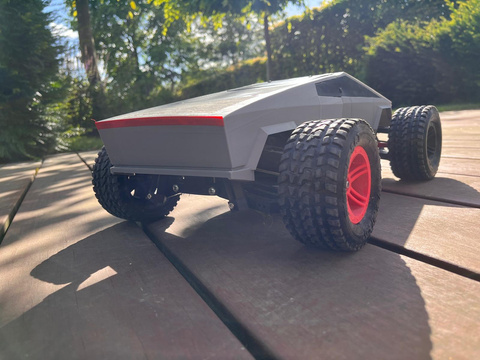
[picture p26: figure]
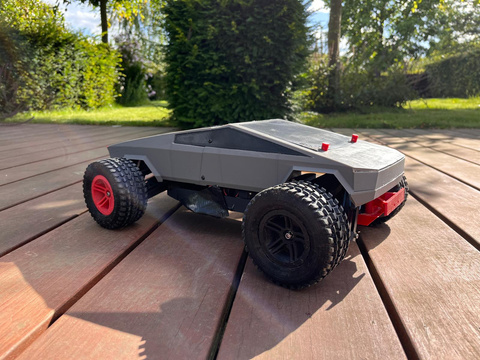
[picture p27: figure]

THESE ARE CRUCIAL
STEPS BECAUSE WHEN
YOU OPEN OR
DISASSEMBLE THE
CAR IN THE FUTURE,
THESE WILL ALWAYS
BE THE FIRST THINGS
YOU’LL NEED TO
HANDLE.
SO, IT’S IMPORTANT
TO KNOW HOW TO DO
THEM CORRECTLY.
TAKE YOUR TIME AND
ENSURE EVERYTHING
IS DONE PROPERLY.
GOOD LUCK!

# STEP 1

WE BEGIN THE FINAL STEP
BY ATTACHING THE
BUMPER. THIS PART IS 3D-PRINTED USING TPU, AN
ELASTIC FILAMENT THAT IS
PERFECT FOR ABSORBING
IMPACTS—LIKE WHEN YOU
CRASH HARD INTO A POLE.
SECURE THE BUMPER TO
THE FRONT OF THE CAR BY
SCREWING IT INTO THE
FOUR PRE-DRILLED HOLES
AT THE BACK USING 8MM
SCREWS. THESE SHOULD BE
TIGHTENED FIRMLY.

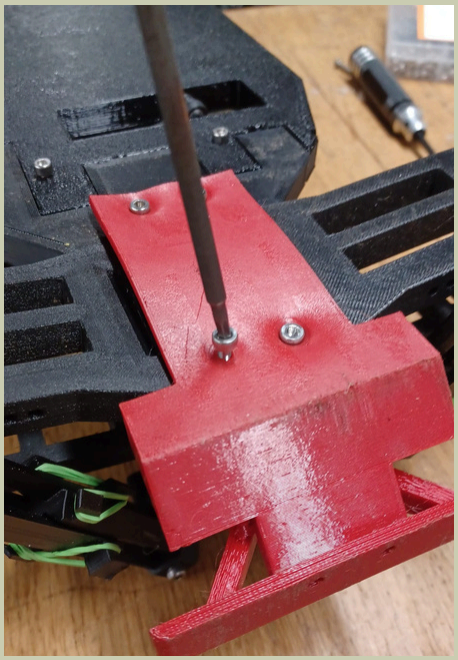
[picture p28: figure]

# almost

# there

# STEP 2

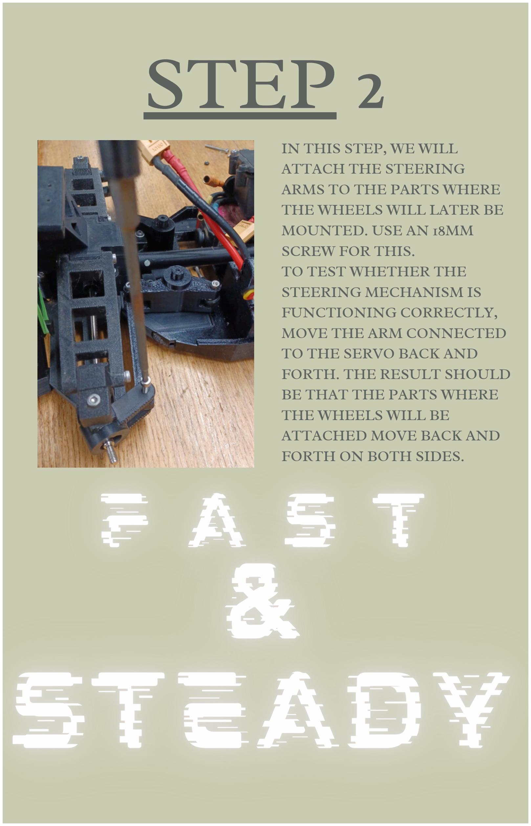
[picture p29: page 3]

IN THIS STEP, WE WILL
ATTACH THE STEERING
ARMS TO THE PARTS WHERE
THE WHEELS WILL LATER BE
MOUNTED. USE AN 18MM
SCREW FOR THIS.
TO TEST WHETHER THE
STEERING MECHANISM IS
FUNCTIONING CORRECTLY,
MOVE THE ARM CONNECTED
TO THE SERVO BACK AND
FORTH. THE RESULT SHOULD
BE THAT THE PARTS WHERE
THE WHEELS WILL BE
ATTACHED MOVE BACK AND
FORTH ON BOTH SIDES.

# STEP 3

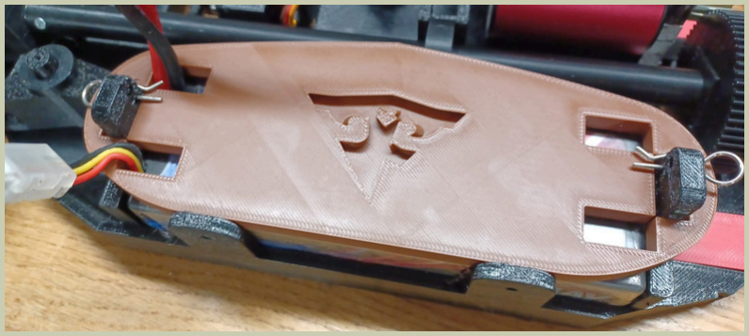
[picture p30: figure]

SLIDE THE BATTERY HOLDER ONTO THE PINS USING THE TWO MIDDLE HOLES. THE OTHER HOLES ARE DESIGNED FOR THE BATTERY CABLES, ALLOWING THE BATTERY TO BE POSITIONED IN EITHER DIRECTION. YOU CAN SECURE THE HOLDER BY INSERTING THE FASTENING PINS, SHOWN IN THE PHOTO, INTO THE LOWEST POSSIBLE HOLE TO ENSURE THE HOLDER STAYS FIRMLY IN PLACE.

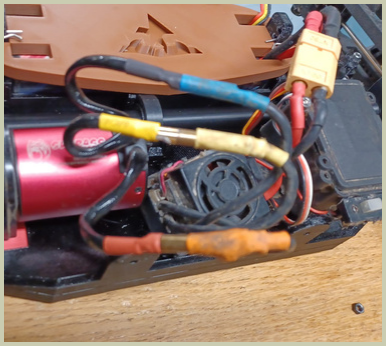
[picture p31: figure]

NOW, CONNECT THE MOTOR
CABLES TO THE ESC CABLES BY MATCHING THE COLORS—EACH
COLOR SHOULD CONNECT TO ITS CORRESPONDING COLOR. THE
MOTOR CABLE SHOULD ALSO BE PLUGGED INTO THE
CORRESPONDING ESC CABLE.
THIS IS ALSO HOW YOU WILL
CONNECT THE BATTERY, BUT
DON’T DO THIS JUST YET TO
AVOID DRAINING THE BATTERY.

# STEP 4

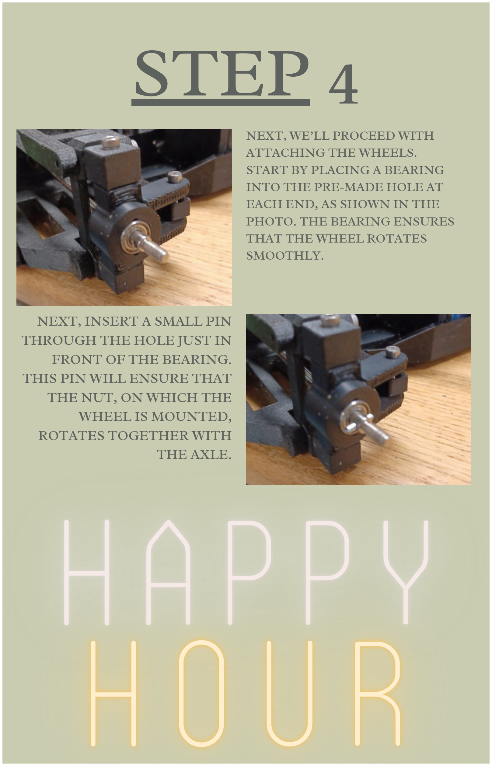
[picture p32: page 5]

NEXT, WE’LL PROCEED WITH
ATTACHING THE WHEELS.
START BY PLACING A BEARING INTO THE PRE-MADE HOLE AT
EACH END, AS SHOWN IN THE
PHOTO. THE BEARING ENSURES THAT THE WHEEL ROTATES
SMOOTHLY.

NEXT, INSERT A SMALL PIN
THROUGH THE HOLE JUST IN
FRONT OF THE BEARING.
THIS PIN WILL ENSURE THAT
THE NUT, ON WHICH THE
WHEEL IS MOUNTED,
ROTATES TOGETHER WITH
THE AXLE.

# STEP 5

NOW, SLIDE THE HEXAGONAL
NUT ONTO THE PIN. THE
INNER PART OF THE WHEEL
WILL FIT PERFECTLY ONTO
THIS NUT, ALLOWING IT TO
ROTATE TOGETHER WITH
THE NUT.

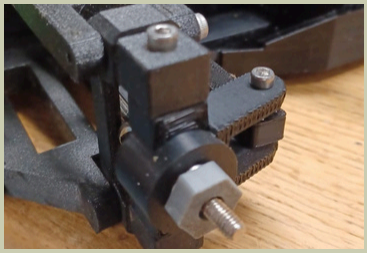
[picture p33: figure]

NEXT, SLIDE THE 3D-PRINTED WHEEL ONTO THE
HEX NUT. THIS WHEEL IS
ALSO PRINTED FROM A
FLEXIBLE FILAMENT,
PROVIDING EXCELLENT GRIP
ON THE GROUND AND GOOD
SHOCK ABSORPTION, WHICH
HELPS REDUCE THE IMPACT

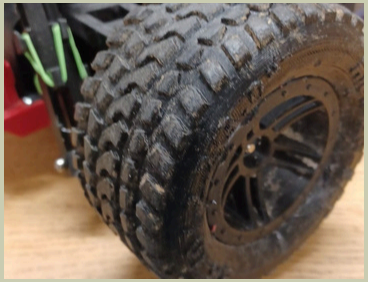
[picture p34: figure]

DURING HARD COLLISIONS. FINALLY, SCREW THE 7MM NUT ONTO THE BACK OF THE
WHEEL USING THE SPECIAL
SCREWDRIVER. THIS NUT
WILL HOLD THE WHEEL
SECURELY IN PLACE.THE
TIGHTER YOU SCREW IT, THE
BETTER IT WILL HOLD THE
WHEEL IN PLACE.

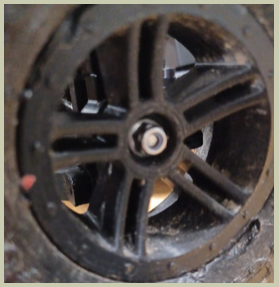
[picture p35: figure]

# Already rollin

’!

# STEP 6

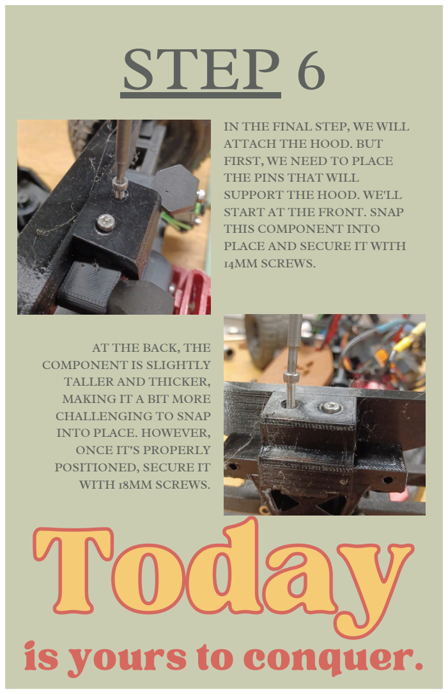
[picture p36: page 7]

IN THE FINAL STEP, WE WILL
ATTACH THE HOOD. BUT
FIRST, WE NEED TO PLACE
THE PINS THAT WILL
SUPPORT THE HOOD. WE'LL
START AT THE FRONT. SNAP
THIS COMPONENT INTO
PLACE AND SECURE IT WITH
14MM SCREWS.

AT THE BACK, THE
Today

COMPONENT IS SLIGHTLY
TALLER AND THICKER,
MAKING IT A BIT MORE
CHALLENGING TO SNAP
INTO PLACE. HOWEVER,
ONCE IT’S PROPERLY
POSITIONED, SECURE IT
WITH 18MM SCREWS.

is yours to conquer.

# STEP 7

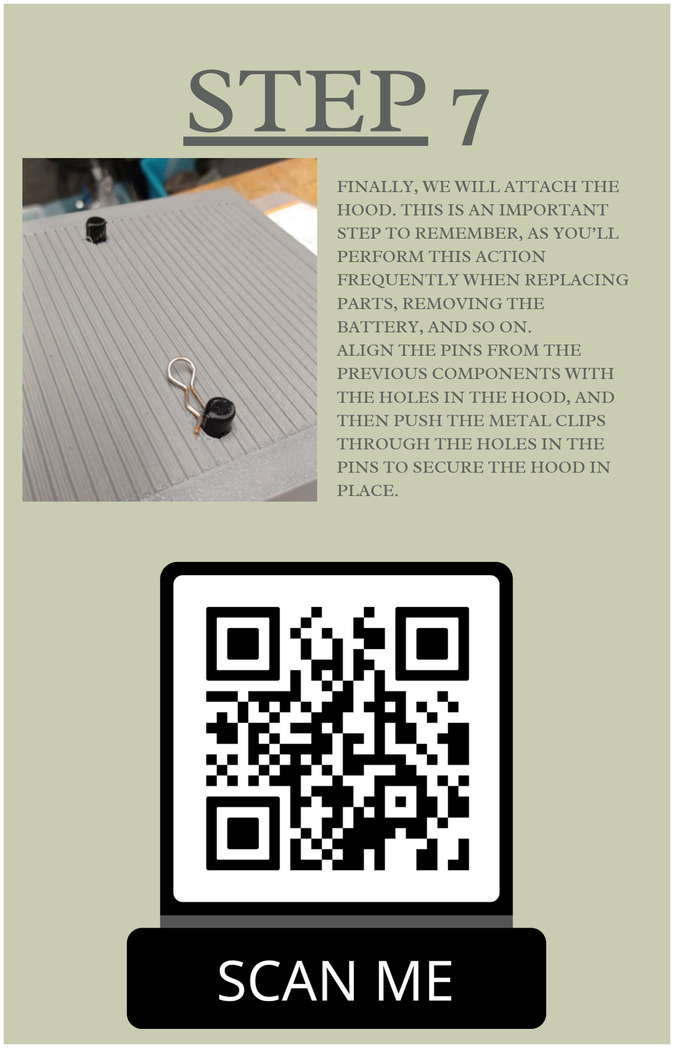
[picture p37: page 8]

FINALLY, WE WILL ATTACH THE HOOD. THIS IS AN IMPORTANT STEP TO REMEMBER, AS YOU’LL PERFORM THIS ACTION
FREQUENTLY WHEN REPLACING
PARTS, REMOVING THE
BATTERY, AND SO ON.
ALIGN THE PINS FROM THE
PREVIOUS COMPONENTS WITH
THE HOLES IN THE HOOD, AND THEN PUSH THE METAL CLIPS
THROUGH THE HOLES IN THE
PINS TO SECURE THE HOOD IN PLACE.

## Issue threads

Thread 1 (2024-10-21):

Motor Mount overal uitverkocht

arnobonte, 2024-10-21:
De "Reely 536014C Reserveonderdeel Motorhouder" uit de BoM is overal uitverkocht (conrad, bol, amazon, ...). Kent er iemand een alternatief voor dit onderdeel?

frederikanrys, 2024-10-21:
Dat is jammer. Ik heb er nog liggen. Als je me je adres geeft zal ik er eentje opsturen. Nog iets anders nodig?

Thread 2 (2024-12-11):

Missing driveshaft connector on the off-the-shelf parts list

thomasbonte, 2024-12-11:
I miss the actual driveshaft connector (not differential) in the parts list. So the one that holds the bearings. Possibly the link in the parts link is wrongly referring to the differential.

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

frederikanrys, 2024-12-12:
I created it myself using a 5mm metal bar

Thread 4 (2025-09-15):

Dog bone quality issue

thomasbonte, 2025-09-15:
The OTS dog bone part as sold on [Amazon.de](https://www.amazon.de/-/en/dp/B08FMJXFCH?psc=1&ref=ppx_yo2ov_dt_b_product_details) fails too fast. The build quality of seems to be too low. We need to find another source.

thomasbonte, 2025-09-15:
Maybe [this one](https://nl.aliexpress.com/item/1005003168312581.html?gatewayAdapt=glo2nld) is a candidate, but need to check if the dimensions are the same. It does hold the same version number: 108015 Keywords searched for: 108015 Universal Axle HSP Truck

thomasbonte, 2025-10-07:
Apparently the small bearing was broken which caused the dog bone to break. Once fixed, the dogbone is holding just fine.

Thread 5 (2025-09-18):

BOM missing servo linkage

thomasbonte, 2025-09-18:
Unless I stupidly miss it, I don't find the servo linkage in the BOM.
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

thomasbonte, 2025-10-07:
Unfortunately, the found steering linkage was too bulky as the plastic touches with driveshaft when the servo is at its maximum position. Searching for a less bulky one.

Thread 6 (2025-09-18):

Motor Mount not available

thomasbonte, 2025-09-18:
The motor mount as listed in the BOM is nowhere available anymore for purchase. Need to find a solution for this, as it's a crucial piece.

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

thomasbonte, 2025-09-18:
Link to the sold out item: https://www.conrad.be/nl/p/reely-536014c-reserveonderdeel-motorhouder-1418556.html

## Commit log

2024-02-25 added steering
2024-02-26 added bearings
2024-02-27 removed wrong bearing
2024-04-23 Added info on motor, mount and wheels
2024-05-02 moved into directories added wheel
    [Nonhex.3mf]
2024-05-08 adding shocks
    [Body.stl, Body.stp, Bottom.stl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]
2024-05-08 updating plate
2024-05-08 drivetrain files
2024-05-21 fixed wheel
2024-05-21 Added exported STL files
    [diff-exploded.stl, driveshaft-central.stl, driveshaft-connect.stl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]
2024-05-21 Adding plate rear
    [plate-center.stl, plate-rear-bottom.stl]
2024-05-21 some renames
    [turn-front-left-caster.stl, turn-front-left-knuckle.stl, wing-front-left-bottom.stl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]
2024-05-21 Updated the plate with stronger connectors
    [plate-center.stl, plate-front-bottom.stl, plate-rear-bottom.stl]
2024-05-22 updated the wheel internal witdh to 1.5 mm
2024-06-02 diff case connector moved, servo moved, battery on plate, added bearing holder
    [plate-center.stl, plate-front-bottom.stl, plate-rear-bottom.stl]
2024-06-02 Added bearing
2024-06-02 Added hex files
    [hex.stl]
2024-06-02 added screw to driveshaft connector
    [driveshaft-connect-with-screw.stl]
2024-06-02 Added a bumper and update holes in the plate
    [Bumper.stl, plate-diff-top.stl, plate-front-bottom.stl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]
2024-06-03 Updated Turn
    - Stronger
    - Single claw can be used for both fixed and turning parts
    - Ball-bearing are easier to insert
    - Easier to remove ball-bearings
    - 45deg corners for printing under an angle
    [Turn.stl]
2024-06-05 minor mods to stl files
    [driveshaft-connect-with-screw.stl, driveshaft-connect.stl, hex.stl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]
2024-06-11 Reduced space between bearing from 2mm to 1.8mm
    - Reduced pocket for small bearing accordingly
    [Turn.stl]
2024-06-11 Made claw visible
    [Turn.stl]
2024-06-14 Added Shock, SteerArm and DiffBracket
    [DiffBracket.stl, Shock.stl, SteerArm.stl]
2024-06-15 updated hex, updated turn, renamed some files
    [Turn.stl, diff-bracket.stl, steering-arm.stl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]
2024-06-16 upgraded differential
    [diff-exploded-strong.stl, diff-exploded.stl]
2024-06-16 wheel tire update
2024-06-17 Improved shock stop
    [Shock.3mf, Shock.stl]
2024-06-17 Added steer arms in diifferent lengths
    [SteerArm.3mf, SteerArm.stl]
2024-06-19 Added initial BOM
    [BOM.xlsx]
2024-06-20 Added links to pinion, dogbones and battery
    [BOM.xlsx]
2024-06-20 Added gear svg, dxf and shapr documents
    [gears.dxf]
2024-06-21 flexible drive shaft update
    [driveshaft-central-pla.stl, driveshaft-central-tpu.stl, driveshaft-central.stl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]
2024-06-21 updated bom for driveshaft
    [BOM.xlsx]
2024-06-21 move gear to util folder
    [gears.dxf]
2024-06-21 driveshaft update
    [driveshaft-central-pla.stl, driveshaft-central-tpu.stl, driveshaft-cover.stl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]
2024-06-23 steering and hex update
    [Shock.3mf, SteerArm.3mf, SteerArm.stl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]
2024-07-05 added steering rings
    [steering-rings.stl]
2024-07-05 plate updates with bigger motor hole, diff top reeinforced and attachments for the cubertruck
    [plate-center.stl, plate-diff-top.stl]
2024-07-05 cybertruck body
    [Cybertruck-front-holder.stl, Cybertruck-front.stl, Cybertruck-lights.stl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]
2024-07-05 cybertruck body - small fixes
    [Cybertruck-front-holder.stl, Cybertruck-rear.stl]
2024-07-07 cybertruck body - holder update
    [Cybertruck-front-holder.stl, Cybertruck-rear-holder.stl]
2024-07-13 switch to new differential
    [Bumper.stl, diff-bracket.stl, diff-exploded.stl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]
2024-07-15 steering arm to 67 mm
    [steering-arm-67mm.stl, steering-arm-72mm.stl]
2024-07-19 plate change - connection to rear shell - decal added and making print friendly uploaded shapr stl files
    [Cybertruck-decal.stl, Cybertruck-front.stl, Cybertruck-rear.stl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]
2024-07-26 Reworked BOM into Markdown
    [BOM.xlsx]
2024-07-26 Indicated steering stash
2024-07-27 Fresh prints!
2024-07-28 Fresh prints
2024-08-08 cyber truck decal from 0.2mm to 0.6mm
    [Cybertruck-decal.stl]
2024-08-08 BOM update
2024-08-11 bom update + cybertruck logo
    [Cybertruck-logo.stl]
2024-08-13 manual + battery holder
    [plate-battery-holder.stl]
2024-08-14 Added 20 top wings in TPU
2025-11-15 Remove old files
    [Bumper.stl, diff-exploded.stl, driveshaft-central-pla.stl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]
2025-11-29 v2: Add Traxxas Slash 4x4 compatible parts list with prices
    - New README with v2 drivetrain using off-the-shelf Traxxas Slash 4x4 parts
    - Added price indications for all components (~€77 total estimated cost)
    - Parts include metal differentials, CVD driveshafts, slipper clutch, bearings
    - Moved original v1 design files to archive/ folder for reference
    [Body.stl, Body.stp, Bottom.stl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]
2025-12-05 Add new STL exports with original design files
    New printable parts:
    - Plate components: diff-front/rear (top/bottom), mid-front, mid-rear
    - Steering components: left, right, top, connect, rings
    - Turn components: caster, front, rear
    - Battery holder
    Original design files included in files/originals/ (Plate, Steering, Turn)
    [Plate.x_b, Steering.x_b, Turn-caster.stl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]
2025-12-05 Update README with complete parts list and add missing STL files
    - Add Motor & Electronics section (motor, ESC, pinion, battery, servo)
    - Reorganize parts into Fasteners & Hardware section
    - Add printed parts list with all STL file references
    - Add optional printed parts section (wheels, shocks)
    - Add Extrudr Flex Hard TPU recommendation
    - Add new STL files: bumper, shock, steering-arm, wheels, wings
    - Rename Shock.stl to lowercase
    [bumper.stl, shock.stl, steering-arm-67mm.stl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]
2025-12-05 Remove duplicate Turn files (uppercase versions)
    [Turn-caster.stl, Turn-front.stl, Turn-rear.stl]
2025-12-05 Add lowercase turn component files
    [turn-caster.stl, turn-front.stl, turn-rear.stl]
